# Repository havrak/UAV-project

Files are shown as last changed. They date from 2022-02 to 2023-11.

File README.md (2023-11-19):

# UAV project

This repository contains all resource that comprised my final thesis for my senior year in high school.
Main purpose was to create UAV platform based on Raspberry Pi.

Codebase is this project is rather bad by my current standards and is heavily impacted by the fact it was essentially my first hardware related project.
Not to mention my experience with C++ was rather limited at the time.

Desktop client is written in C++ using Gtk3 and is used to control the drone and display telemetry data.
UI wise it's really bad, and code itself doesn't land much in a way for easy rewrite.

Drone side might fare a bit better, but it's still not great.
Usage of threads is rather questionable and OOP design patterns were a hip new thing for me at the time and not something I was able to use properly.

Thus some parts of codebase are overengineered and some lack any flexibility and don't deserve much other than deletion.

In my 3rd semester of university I've made addition to this project in a shape of proper custom PCB to house drone electronics.

I might rewrite this project in the future, but time is a limited resource and school+work take priority.
Though if rewrite happens, it will be wholly different project.
* camera streaming with gstreamer has never worked as well as I wanted it to
* using Wi-Fi for communication was never ideal (drone was acting as AP)
* codebase and communication protocol needs to be much more open to allow different configurations of hardware
* desktop client needs to be rewritten from scratch and preferably in Qt
* way more robust compilation and deployment process is needed (Kconfig, hierarchical Makefiles, etc.)

# Libraries and toolkits
* [WT901B library](https://github.com/havrak/Raspberry-JY901-Serial-I2C)
* [INA226 library](https://github.com/havrak/raspberry-pi-ina226)
* [PCA9685 library](https://github.com/havrak/PCA9685-rpi)
* [inih (INI Not Invented Here)](https://github.com/benhoyt/inih)
* Gtk3
* crp, fmt
* WiringPi

# Photos

### UAV Photos

whole plane

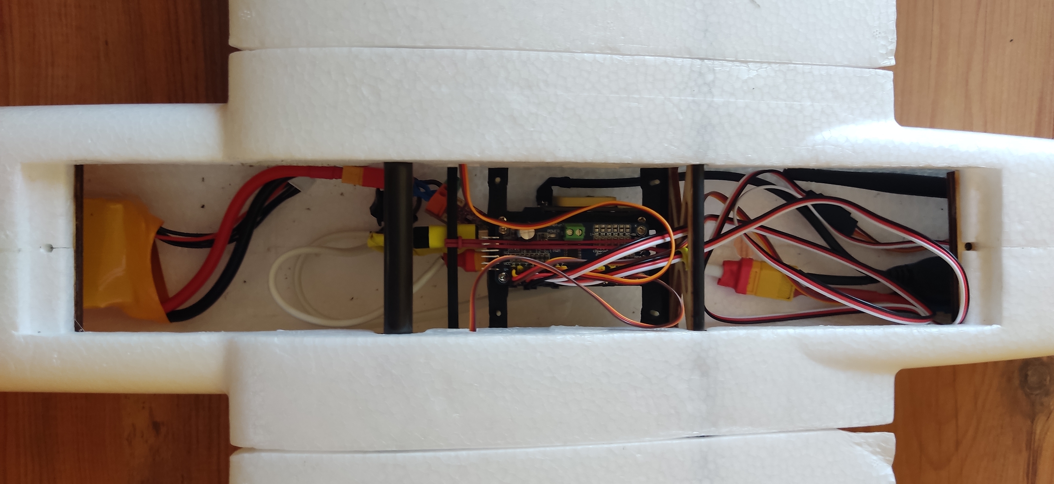
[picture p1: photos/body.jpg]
body detail


### Board

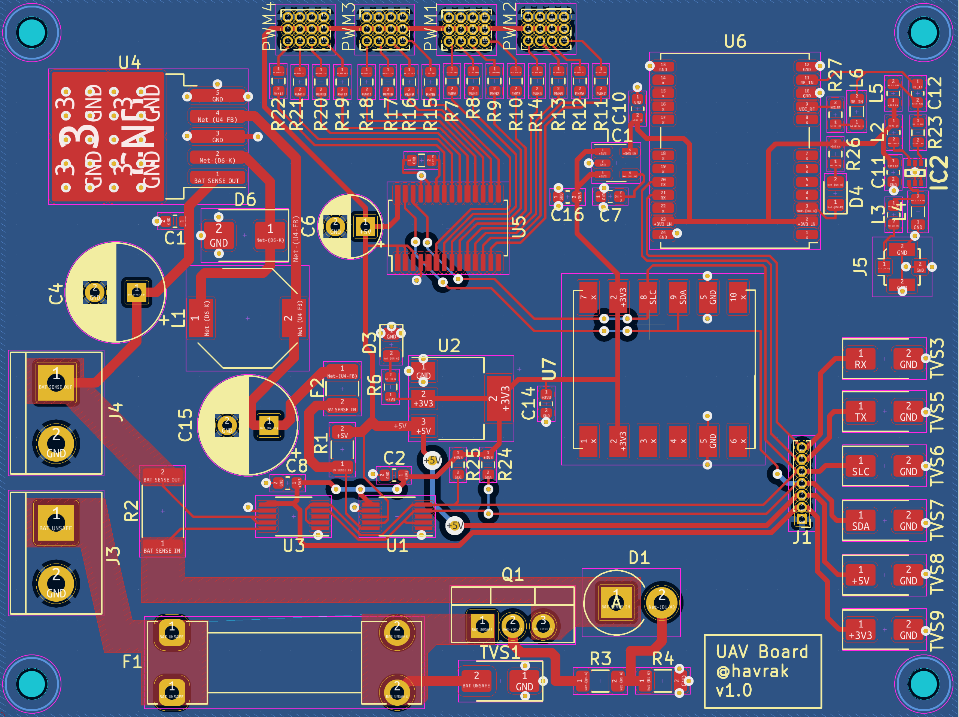
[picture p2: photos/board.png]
board


# Credits
* textures for desktop client originate from [marek-cel/QFlightinstruments](https://github.com/marek-cel/QFlightinstruments)

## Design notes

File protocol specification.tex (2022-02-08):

\documentclass[a4paper,12pt]{report}

\addtolength{\topmargin}{-1.1in}
\setlength\textheight{265mm}
\setlength\textwidth{165mm}
\setlength\oddsidemargin{-2mm}
\setlength\evensidemargin{-2mm}
\usepackage[english]{babel}
\usepackage{tabularx}
\usepackage{longtable}
\usepackage[a-2u]{pdfx}
\usepackage{graphicx}
\usepackage{caption}
\usepackage{lmodern,textcomp}
\usepackage[T1]{fontenc}
\usepackage{fancyhdr}

\def\author{Havránek Kryštof <krystof@havrak.xyz>}

\def\name{UAV Project }

\makeatletter
\def\@makechapterhead#1{
  {\parindent \z@ \raggedright \normalfont
      \huge\bfseries  #1
      \par\nobreak
      \vskip 20\p@
    }}
\def\@makeschapterhead#1{
  {\parindent \z@ \raggedright \normalfont
      \huge\bfseries #1
      \par\nobreak
      \vskip 20\p@
    }}
\makeatother

\renewcommand{\chaptermark}[1]{%
  \markboth{#1}{}}

\fancypagestyle{plain}{
  \fancyhf{}
  \renewcommand{\headrulewidth}{0.4pt}
  \renewcommand{\footrulewidth}{0.4pt}
  \fancyhead[L]{\textbf{\name -- \leftmark}}

  \fancyfoot[L]{\author}
  \fancyfoot[C]{}
  \fancyfoot[R]{\thepage}
}

\begin{document}
\pagestyle{plain}

\chapter{Protocol specification}

\begin{itemize}
  \item protocol desing
    \begin{itemize}
      \item 1st byte -- type of message
      \item 2nd byte -- priority of message (for now for messages with higher priority than 0 new thread will be created)
      \item 3rd and 4th byte -- gives information about size of message -- 3rd is 8 higher bytes, 4th is lower 8 bytes
      \item 5 -- value to be added to check sum -- first 5 bytes need to be divisible by 7
      \item ... -- message
      \item each message is terminated with following sequence -- 0x00, 0x00, 0xFF, 0xFF, 0xFF
    \end{itemize}
  \item ranges
    \begin{itemize}
      \item 0x00 -- 0x20 -- settings management
      \item 0x21 -- 0x40 -- control
      \item 0x41 -- 0xFF -- telemetry
    \end{itemize}
	\item * symbol means code is only used as get request/confirmation
	\item structures used are specified in \verb|<protocol_spec.h>|
\end{itemize}

\subsubsection{Settings}

\begin{center}
  \begin{longtable}{| m{1cm} | m{1.5cm} | m{13cm} | }
    \hline
    0x01 & PI+CL & ping -- empty message send by both sides \\
    0x02 & CL    & restart of system                        \\
    0x03 & CL    & shutdown                                 \\
    0x04 & CL    & disconnect client                        \\
    0x08 & CL    & camera settings                          \\

    \hline
  \end{longtable}
\end{center}

\subsubsection{Control}

\begin{itemize}
  \item these messages are only send by the client to raspberry pi
  \item standart control message will be send continuously -- every few milliseconds (client will have counter to prevent overloading of the server)
  \item we are fine with few of these messages getting lost, as even minor movements will probably result in new message getting send
  \item special message will send confirmation to the client
    \begin{itemize}
      \item client will add these messages to queue, which will be scanned from time to time
      \item if response from server wasn't received in some time client will resend the message
    \end{itemize}

\end{itemize}

\begin{center}
  \begin{longtable}{| m{1cm} | m{1.5cm} | m{13cm} | }
    \hline
    0x21 & CL+PI* & standart control message -- status of analog joystick and shoulder buttons                                                              \\
    0x22 & CL+PI* & special control event -- generated by pressing buttons that don't directly control control surfaces, but are free for further additions \\
    \hline
  \end{longtable}
\end{center}

\subsubsection{Telemetry}

\begin{itemize}
  \item all telemetry, except pwm settings,  is send in intervals
  \item if client want new data immediately it can send message with same header
  \item in such case using priority option is advisable
  \item range above 0x80 is used for errors
\end{itemize}

\begin{center}
  \begin{longtable}{| m{1cm} | m{1.5cm} | m{13cm} | }
    \hline
    0x41 & PI*+CL & status of all i/o                        \\
    0x42 & PI*+CL & general packet including all information \\
    0x43 & PI*+CL & attitude sensor and GPS                  \\
    0x44 & PI*+CL & battery status (reading from ina226)     \\
    0x45 & PI*+CL & pwm setting on servo driver              \\
    0x81 & PI     & general error message                    \\
    \hline
  \end{longtable}
\end{center}

\end{document}

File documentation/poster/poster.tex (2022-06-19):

\documentclass[final]{beamer}

\usepackage[T1]{fontenc}
\usepackage[czech]{babel}
\usepackage{lmodern}
\usepackage[size=a3paper,scale=1.2]{beamerposter}
\usetheme{gemini}
\usecolortheme{mit}
\usepackage{graphicx}
\usepackage{booktabs}
\usepackage{tikz}
\usepackage{pgfplots}
\usepackage{subfigure}
\pgfplotsset{compat=1.14}

% ====================
% Lengths
% ====================

% If you have N columns, choose \sepwidth and \colwidth such that
% (N+1)*\sepwidth + N*\colwidth = \paperwidth
\newlength{\sepwidth}
\newlength{\colwidth}
\setlength{\sepwidth}{0.025\paperwidth}
\setlength{\colwidth}{0.3\paperwidth}

\newcommand{\separatorcolumn}{\begin{column}{\sepwidth}\end{column}}

% ====================
% Title
% ====================

\title{Maturitní práce -- Bezpilotní letadlo}

\author{Havránek Kryštof (Programování, 4.E)}

\institute[shortinst]{Gymnázium, Praha 6, Arabská 14}

% ====================
% Footer (optional)
% ====================

\footercontent{
  \href{https://github.com/havrak/UAV-project}{https://github.com/havrak/UAV-project} \hfill
  Březen 2022 \hfill
  \href{mailto:krystof@havrak.xyz}{krystof@havrak.xyz}}
% (can be left out to remove footer)

% ====================
% Logo (optional)
% ====================

% use this to include logos on the left and/or right side of the header:
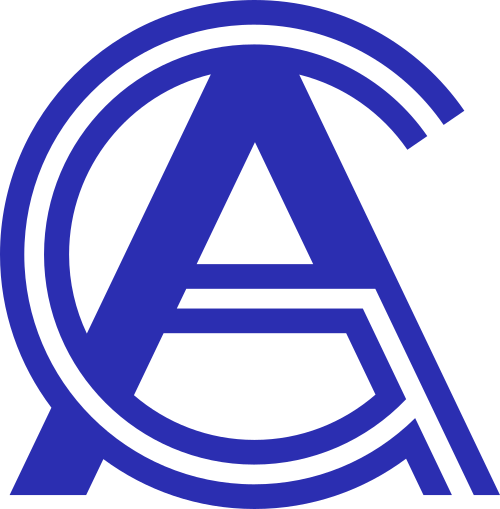
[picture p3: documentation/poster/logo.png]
\logoleft{}
% \logoleft{\includegraphics[height=7cm]{logo2.pdf}}

% ====================
% Body
% ====================

\begin{document}

\begin{frame}[t]
  \begin{columns}[t]
    \separatorcolumn

    \begin{column}{\colwidth}

      \begin{block}{Abstrakt}

        Cílem práce je vytvoření bezpilotního letadla a doprovodného systému umožnující pilotovi letadlo dálkově ovládat.
        Pilot by měl mít možnost sledovat živý přenos z kamery a získávat doprovodnou telemetrii.
        Celý program by měl být rychlý, aby ovládání bylo s co nejmenší odezvou, a napsaný stylem umožnující další vývoj.

      \end{block}

      \begin{block}{Použité technologie}

        \begin{figure}
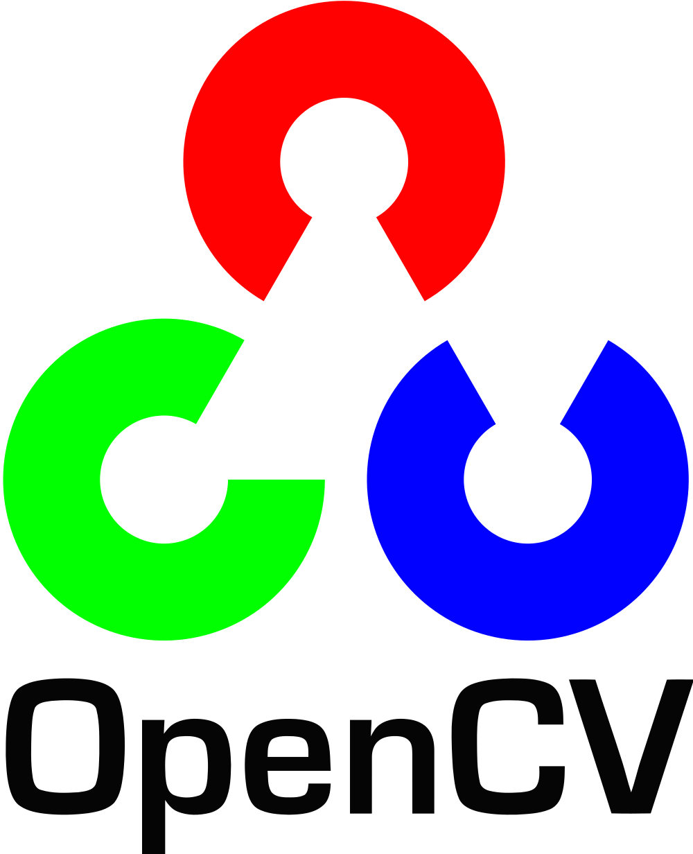
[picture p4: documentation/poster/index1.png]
          \subfigure{}
          \hfill
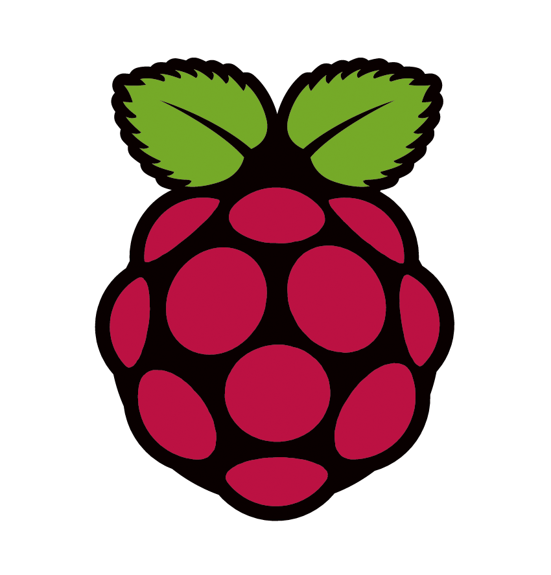
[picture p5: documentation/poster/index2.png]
          \subfigure{}
          \hfill
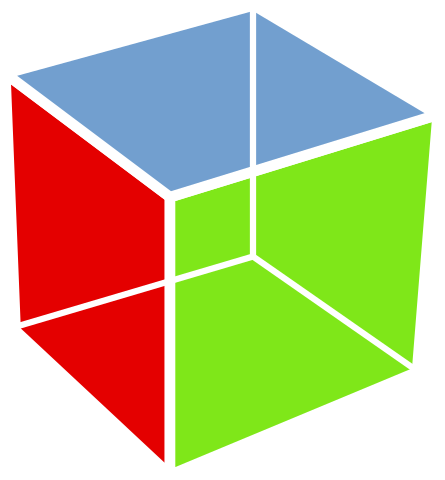
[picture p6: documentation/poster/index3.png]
          \subfigure{}
          \hfill
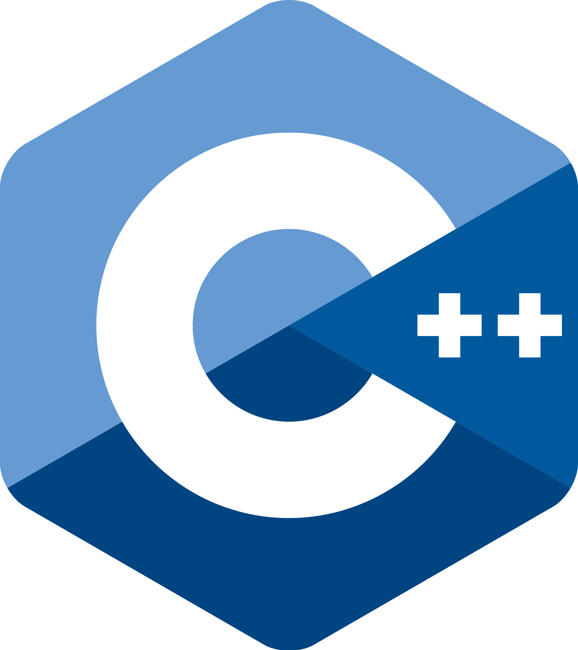
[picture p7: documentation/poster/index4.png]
          \subfigure{}
          \hfill
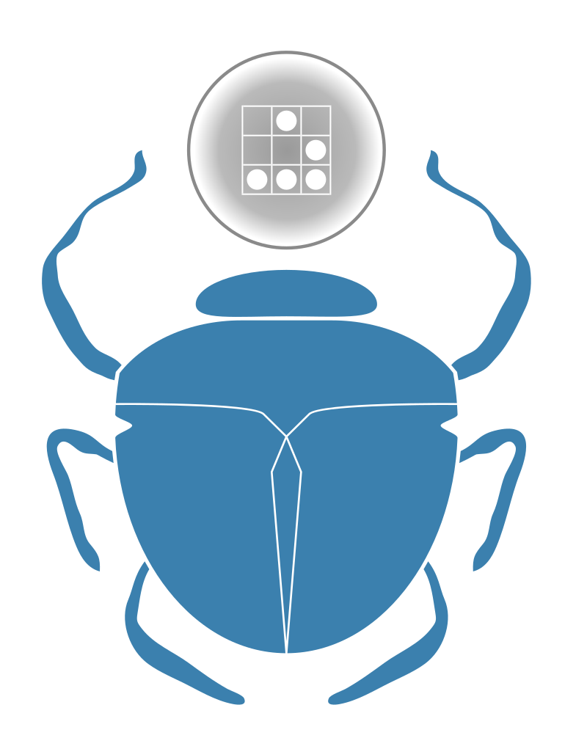
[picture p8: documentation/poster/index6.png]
          \subfigure{}
          \hfill
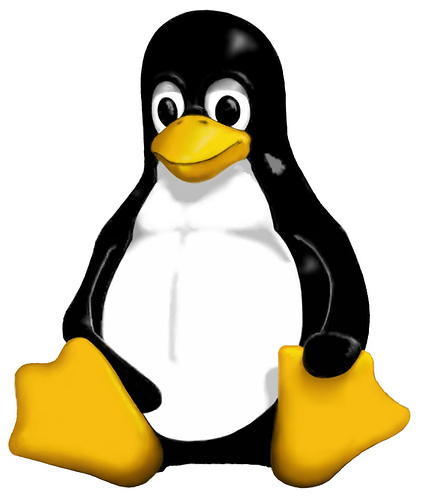
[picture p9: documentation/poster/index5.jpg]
          \subfigure{}
          \hfill

        \end{figure}

			Celý projekt je psán v jazyce C++ a vyvíjen primárně pro zařízení s operačním systémem Linux.
			V případě ovládací softwaru je port na další OS možný, jelikož používaný grafický toolikt je multiplatformní.

      \end{block}

      \begin{block}{Komunikační protokol}

				Obě části projektu mezi sebou komunikují prostřednictvím protokolu postaveném na rodině TCP.
				Letadlo na sebe přejímá roli serveru, umožňuje tak několik clientů -- telemetrii z dronu lze tak monitorovat z několika počítačů.
				Případně si lze \uv{předávat} kontrolu nad dronem mezi počítači.

				Protokol se stará o tři důležité části řízení letadla.
				Je schopen na dálku drona konfigurovat -- například spustit kameru.
				Dále předává informace letadlu z herního, kterým se letadlo ovládá.
				V neposlední řadě umožňuje letadlu posílat zpět telemetrii, případě chybové hlášky.
				Telemetrie se pak zobrazuje pilotu v ovládacím softwaru, chybové hlášky se manifestují prostřednictvím dialogových oken.
      \end{block}

      \begin{block}{Fotografie letadla}

				\begin{figure}[h]
					\centering
					
				\end{figure}

      \end{block}

    \end{column}

    \separatorcolumn

    \begin{column}{\colwidth}

      \begin{block}{Hardware a software letadla}

				Dron je postaven na jednodeskovém počítači Raspberry Pi.
				Systém je primárně určen pro moduly ze série Raspberry Pi Zero.
				Primárně se však tak je činěno z důvodu prostorových omezení řad koster letadel.
				Teoreticky může projekt fungovat na libovolném počítači Raspberry Pi.

				Jelikož používá specifické funkce pro interakci s hardwarem není možné projekt rozeběhnout na dalších malých počítačích.
				Stejně tak je projekt závislý na knihovnách a driverech, které jsou standardní součástí operačního systému raspbian.

				Projekt využívá hned několik periférií, těma jsou:

        \begin{enumerate}
          \item WT901B -- devíti-osý polohový senzor -- počítá yaw, roll a pitch
          \item PCA9865 -- modul pro ovládání servo motorů
          \item INA226 -- voltmetr/ampérmetr pro získání dat z baterie
					\item ublox NEO 7M GPS -- GPS modul
					\item Beatles 40A ESC -- Electronic Speed Control -- umožňuje ovládat hlavní motor
        \end{enumerate}

      \end{block}

      \begin{block}{Schéma zapojení}

				Schéma zapojení je relativně přímočaré.
				Většina komponent s Raspberry PI komunikuje prostřednictvím I2C spojený a je napojena na piny 3 a 5.
				Vzhledem k počtu komponent jsou napojené na 3.3V drain přes 4.7 $\Omega$ rezistory.
				Výjimku představuje GPS, která využívá sériovou linku.

				Raspberry Pi a další sensory nejsou napájené prostřednictvím ESC, ale z přímo baterie prostřednictvím DC/DC step down covertru.

				\begin{figure}[h]
					\centering
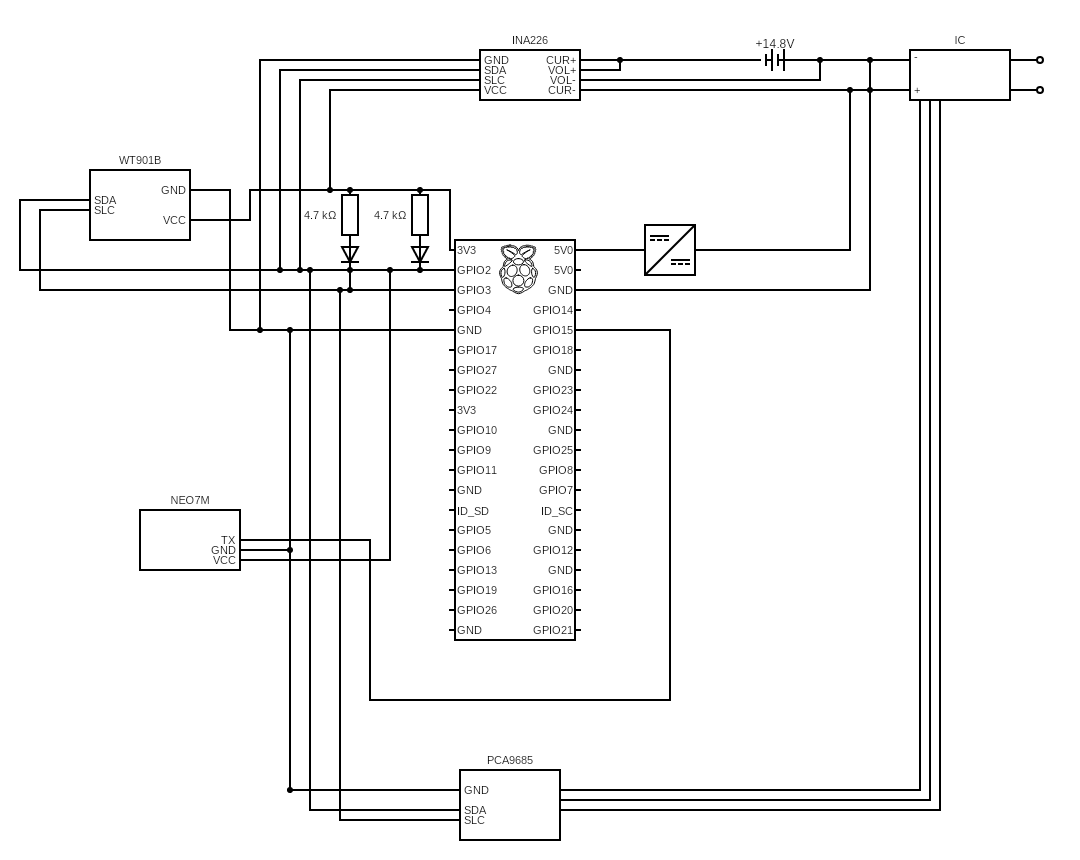
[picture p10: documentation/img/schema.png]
					
				\end{figure}

      \end{block}

    \end{column}

    \separatorcolumn

    \begin{column}{\colwidth}

			\begin{block}{Zapojení}

				Většina komponent je umístěna na pájivém poli, které se přímo nasazuje na samotné Raspberry Pi.
				Voltmetr se nachází v ocasní části letadla, je tak separátně od většiny komponent a připojuje se k nim prostřednictvím USB konektoru.

				K Raspberry Pi je také připojen Wi-Fi Adaptér, který poskytuje silnější signál než integrovaný Wi-Fi čip.
				To jest potřeba, jelikož dron funguje jako router.

				\begin{figure}[h]
					\centering
					
				\end{figure}

			\end{block}

			\begin{block}{Ovládání}

				Letadlo se ovládá pomocí ovladače od herní konzole Xbox One.
				Poloha prvků ovladače je posílána přímo na letadlo, kde se teprve interpretuje.
				Nejprve se přepočítají polohy joysticků na čtverec a pak se vyvodí polohy 4 ovládacích ploch (2 $\times$ aileron, 2 $\times$ ruddervator)

				\underline{Autopilot:}

				Letadlo je schopno držet svojí letovou hladinu bez zásahu pilota.
				K tomu slouží jednoduchý autopilot postavený na dvou PID (proporčně-integračně-derivačních) kontrolérech.
				Jeden se snaží minimalizovat yaw letadla, druhý pak jeho pitch.

			\end{block}

      \begin{block}{Software pro řízení letadla}

			\begin{columns}[T]
				\begin{column}{.4\textwidth}
					Dron se řídí prostřednictvím jednoduché aplikace pro počítač.
					Grafické prostředí je psáno s pomocí knihovny Gtk3, dobře tak ladí s většinou dalších oken na Linuxu.
					Aplikace aktuálně pouze zobrazuje telemetrii z dronu a záznam z jeho kamery.
					Další funkce nebyly zatím implementovány.

				\end{column}
				\begin{column}{.6\textwidth}
			\begin{figure}[h]
				\centering
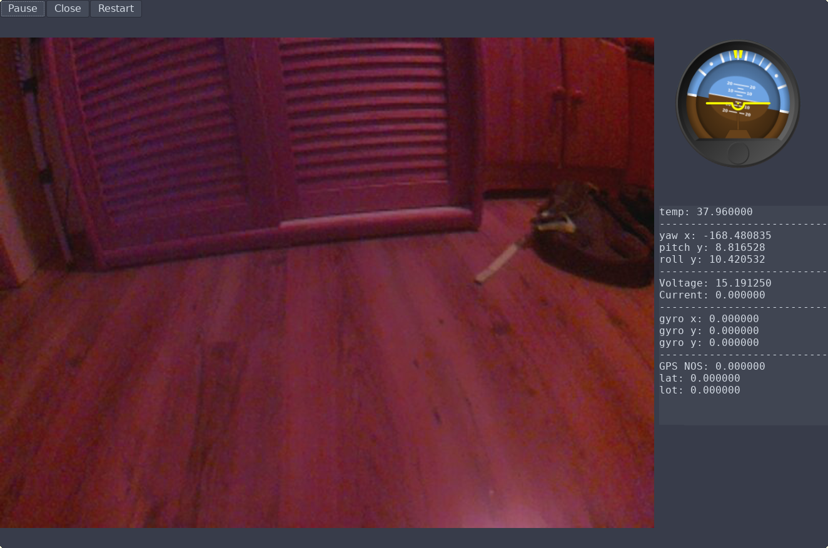
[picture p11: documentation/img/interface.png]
				
			\end{figure}

				\end{column}
			\end{columns}

      \end{block}

    \end{column}

    \separatorcolumn
  \end{columns}
\end{frame}

\end{document}

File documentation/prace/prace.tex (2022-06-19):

\documentclass[a4paper,oneside,12pt]{report}
\setlength\textwidth{155mm}
\setlength\textheight{247mm}
\setlength\topmargin{-10mm}
\setlength\headheight{0mm}
\setlength\oddsidemargin{05mm}
\setlength\evensidemargin{05mm}
\let\openright=\clearpage

%% Vytváříme PDF/A-2u
\usepackage[a-2u]{pdfx}

%% Přepneme na českou sazbu a fonty Latin Modern
\usepackage[czech]{babel}
\usepackage[utf8]{inputenc}
\usepackage{lmodern}
\usepackage[T1]{fontenc}
\usepackage{textcomp}

\usepackage{amsmath}						% rozšíření pro sazbu matematiky
\usepackage{amsfonts}						% matematické fonty
\usepackage{amsthm}							% sazba vět, definic apod.
\usepackage{bbding}							% balíček s nejrůznějšími symboly (čtverečky, hvězdičky, tužtičky, nůžtičky, ...)
\usepackage{bm}									% tučné symboly (příkaz \bm)
\usepackage{graphicx}						% vkládání obrázků
\usepackage{fancyhdr}						% možnost stylizovat záhlaví
\usepackage{fancyvrb}						% vylepšené prostředí pro strojové písmo
\usepackage{indentfirst}				% zavede odsazení 1. odstavce kapitoly
\usepackage[nottoc]{tocbibind} 	% zajistí přidání seznamu literatury,
\usepackage{icomma}         		% inteligentní čárka v matematickém módu
\usepackage{dcolumn}        		% lepší zarovnání sloupců v tabulkách
\usepackage{booktabs}       		% lepší vodorovné linky v tabulkách
\usepackage{paralist}       		% lepší enumerate a itemize
\usepackage{caption}						%	popisky
\usepackage{dirtree}						% strom souborů
\usepackage{minted} 						% vkládání kódu
\usepackage[bottom]{footmisc}  	% poznámky pod čarou vespod
\usepackage{bibentry} 					% citace přes celé heslo, používáno u první citace z jednoho zdroje
\usepackage{xurl}								% umožní url zalomit všude
\usepackage{hyperref} 					% odstranění červených okrajů v obsahu
\nobibliography*

\usepackage{color}
\usepackage{natbib}

\definecolor{pblue}{rgb}{0.13,0.13,1}
\definecolor{pgreen}{rgb}{0,0.5,0}
\definecolor{pred}{rgb}{0.9,0,0}
\definecolor{pgrey}{rgb}{0.46,0.45,0.48}
\renewcommand{\baselinestretch}{1.5}
%%% Údaje o práci

\def\NazevSkoly{Gymnázium, Praha 6, Arabská 14}
% Název oboru včetně počátečního 'Obor'.
\def\NazevOboru{Programování}

% Název práce v jazyce práce (přesně podle zadání)
\def\NazevPrace{Bezpilotní letadlo}

\def\NazevPraceShort{Bezpilotní letadlo}
% Název práce v angličtině
\def\NazevPraceEN{Drone}

% Název práce v němčině
\def\NazevPraceDE{Drohne}

% Jméno autora
\def\AutorPrace{Havránek Kryštof 4E}

% Rok odevzdání
\def\RokOdevzdani{2022}
% Měsíc odevzdání
\def\MesicOdevzdani{Březen}

% Vedoucí práce: Jméno a příjmení s~tituly
\def\Vedouci{ing. Daniel Kahoun}

% Nepovinné poděkování (vedoucímu práce, konzultantovi, tomu, kdo
% zapůjčil software, literaturu apod.)
\def\Podekovani{%
  \textbf{Poděkování}
}

% Abstrakt (doporučený rozsah cca 80-200 slov; nejedná se o zadání práce)
\def\Abstrakt{%
Cílem práce je vytvořit autonomní letadlo, které bude pilot dálkově ovládat prostřednictvím softwaru na počítači.
Z letadla bude během provozu dostávat potřebnou telemetrii a přesnos videa.
Software by měl být napsán stylem, který umožňuje budoucí vývoj.
}

\def\AbstraktEN{%
The aim of the work is to create an unmanned aerial vehicle system which will be controled remotely by the pilot from software on a computer.
Pilot should recive all the necessary telemetry in addition to video stream from the aircraft.
Software should be written in a style that allows for future development.
}
\def\AbstraktDE{%
Ziel der Arbeit ist es, ein unbemanntes Luftfahrzeugsystem zu schaffen, das vom Piloten aus der Ferne von einer Software auf einem Computer gesteuert wird.
Der Pilot sollte alle erforderlichen Telemetrie und Videostreams vom Flugzeug erhalten.
Software sollte in einem Stil geschrieben werden, der eine zukünftige Entwicklung ermöglicht.
}
% 3 až 5 klíčových slov (doporučeno), každé uzavřeno ve složených závorkách
\def\KlicovaSlova{%
  (UAV), (Gtk), (C++), (Raspberry Pi zero 2)
}
\def\KlicovaSlovaEN{%
  (UAV), (Gtk), (C++), (Raspberry Pi zero 2)
}
\def\KlicovaSlovaDE{%
  (UAV), (Gtk), (C++), (Raspberry Pi zero 2)
}

%% Balíček hyperref, kterým jdou vyrábět klikací odkazy v PDF,
%% ale hlavně ho používáme k uložení metadat do PDF (včetně obsahu).
\hypersetup{unicode}
\hypersetup{breaklinks=true}
\hypersetup{pdfborder=0 0 0}

%% Definice různých užitečných maker (viz popis uvnitř souboru)
\include{makra}

%% Titulní strana a různé povinné informační strany
\fancypagestyle{plain}{
  \fancyhf{}
  \renewcommand{\headrulewidth}{0.4pt}
  \renewcommand{\footrulewidth}{0.4pt}
  \fancyhead[C]{}
  \fancyhead[L]{Maturitní práce -- \NazevSkoly}
  \fancyhead[R]{\NazevPraceShort}
  \fancyfoot[L]{Vypracoval: \AutorPrace$\,\,$(\NazevOboru)}
  \fancyfoot[C]{}
  \fancyfoot[R]{\thepage}
}

\begin{document}

\include{titulka}

\tableofcontents

\newpage

\include{uvod}
\pagenumbering{arabic}
\setcounter{page}{1}

\chapter{Rozložení práce}

Práci lze rozdělit na dvě základní komponenty.
První část software běží na počítači přes který se bezpilotní letadlo ovládá, druhá na samotném dronu.
Obě části jsou psané v jazyce C++.

Software pro počítač používá grafickou knihovnu Gtk3 a byl vyvíjen primárně na operačním systém Linux.
Gtk3 je multiplatformní toolkit, port na další operační systémy je tak možný a kód je psán stylem, aby toto umožnil.

Jádro samotného dronu představuje malý počítač Raspberry Pi Zero 2.
Vyšší výkon verze Zero 2 není nutný pro fungování, práce může fungovat na libovolném Raspberry Pi.
Program využívá jen zlomek zdrojů  a to jak po stránce paměti, tak výpočetního výkonu.

Obě části mezi sebou komunikují prostřednictvím protokolu založeném na rodině TCP.
Přenos videa je zprostředkovávám pomocí UDP.
Samotné video je kódováno do jpg, v porovnání s dalšími styly přenosu byla u jpg menší latence.

Rychlost latence byla testována pomocí jednoduché aparatury, kde malý kód četl obrazovku, kde byl zobrazen záznam z kamery, a ovládal LED na ESP32.
Systém jednoduše měřil za jak dlouho se na obrazovce objevila rozsvícená dioda (Předem vybraný pixel změnil barvu) poté co skript poslal příkaz k rozsvícení

\section{Komunikační protokol}

Pilotův počítač a Raspberry mezi sebou komunikují prostřednictvím jednoduchého protokolu postaveném na rodině TCP.
Raspberry Pi přebírá roli serveru, to mimo jiné umožňuje, aby bylo letadlo ovládáno z více stanic.

Protokol prozatím není zašifrovaný a nepočítá také s nevalidními daty.
Šifrování však není příliš nutné -- dron a počítač operují na vlastní síti, kde Raspberry Pi funguje jako Wi-Fi Access--Point.
Struktura protokolu ovšem nabízí možnost jednoduše implementovat symetrickou kryptografii.
Ta by byla zcela postačující, její klíče by byly uloženy v konfiguračních souborech programu.

\subsection{Struktura protokolu}

Každý packet začíná hlavičkou o velikosti 5 bytů.

\begin{enumerate}
  \item typ zprávy
  \item priorita -- Program prozatím prioritu nebere v potaz.
  \item 8 horních bitů velikosti zprávy
  \item 8 dolních bitů velikosti zprávy
  \item dopočet do kontrolního součtu -- součet čísel v hlavničce musí být dělitelný sedmi.
\end{enumerate}

Po hlavičce následuje samotná zpráva zakončená posloupností pěti bytů -- 0x00, 0x00, 0xFF, 0xFF, 0xFF.
Zakončovací řetězec slouží pro případ, kdy nějaký packet nedorazí, či příchozí zpráva byla nějak poškozena.
Nastane li tato situace, program postupně čte byty ze socketu a hledá tuto sekvenci.
Maximální délka zprávy je půl kilobytu, samotná data jsou posílána v balíčcích o maximální velikosti 250 bytů.
Omezení velikosti zprávy je zavedeno hlavně kvůli šetření paměti -- program má pro každého klienta vytvořené jedno pole, do kterého se musí vejít celá zpráva.

Protokol funguje na základě posílání struktur, definovaných v \verb|protocol_spec.h|.
Pro odeslání dat je nejprve nutné nahrát data do struktury.
Dále se z těchto dat vytvoří tzv. SendingStructure, které se odešle do thread poolu, ten zprávu eventuálně odešle.
Při přijímání se data načítají do bufferu spojeným s klientem, ze kterého se později zkopírují objektu ProcessingStructure.
Příslušná část programu si pak data přes memcpy opět zkopíruje do příslušné struktury.

Pro příjem a zpracování zpráv slouží dva thread pooly -- SendingThreadPool a ProcessingThreadPool.
Jednotlivé části programu tak nemusí čekat, až se uvolní socket, aby se mohla data odeslat, či čekat na jejich zpracování pro přijetí dalších.
Speciální případem je zpracování příkazů, které přímo ovládají pohyb letadla.
Pro ovládaní existuje samostatné vlákno, které příkazy vykonává sekvenčně.
Také je implementován mechanismus, kde příliš staré příkazy se nevykonají.

Program sleduje aktivitu na socket pomocí příkazu select.
Při běžné provozu tak většina vláken komunikace spí a zátěž není příliš velká.

Z hlediska programové stránky jsou veškeré součásti komunikace implementovány jako singletony.
Program je tak řešen, aby umožnil jednoduše odesílat zprávy z různých částí programu.

\subsection{Specifikace protokolu}

Protokol obsluhuje tři základní části provozu dronu -- nastavení, ovládaní a telemetrie.
Pro nastavení je vyhrazen rozsah od 0x00 po 0x20 a zahrnuje věci, jako je odpojení klienta, nastavení kamery, či restart.

Další kategorii představuje ovládaní, pro které je vyhrazen prostor mezi 0x21 až 0x40.
Projekt implementuje dva základní typy -- standardní ovládaní (pohyb joysticku, atd.) a speciální.
Standardní slouží pro prosté manuální ovládání dronu.
Speciální například resetuje polohoměr, či zapíná autopilota.

Poslední kategorií je telemetrie, která má zbytek rozsahu do 0xFF.
Tu ve standardním chování posílá Raspberry každých pár stovek milisekund.
Pokud klient potřebuje aktuálnější data, může si je vyžádat odesláním zprávy o stejném typu, jako jsou požadovaná data.
Speciální případ představují chybové hlášky, které vyžádat pochopitelně nejdou a pilotovi se zobrazují v dialogovém okně.

\section{Konfigurace}

Některé vlastnosti programu, lze specifikovat v konfiguračním souboru.
Ten se nachází ve složce \verb|$HOME/.config/uav_control/config.ini| u počítačů s operačním systémem postaveným na UNIXu.
Soubor se psán stylem INI, který je lehce čitelný a~vhodný na malý rozsah konfigurace.
Pro zpracování je použita knihovna inih\footnote{\bibentry{inih}}.

Konfigurace je nutná jak na straně pilota, tak na straně dronu.
U pilota se nastavuje například typ ovladače, či port, na kterém má být přijímán záznam z kamery.
Konfigurace na straně dronu určuje například, jaká je orientace polohového senzoru, či rozložení křídel.

V aktuální verzí se konfigurační soubor nevygeneruje sám, program však má definované hodnoty, ke kterým se uchýlí v jeho absenci.

\chapter{Hardware a Raspberry Pi}

Jádro samotného letadla tvoří malý počítač Raspberry Pi Zero 2.
Ostatní periférie jsou: polohový senzor WT901B, voltmetr a ampérmetr INA226, ovladač na serva PCA9865, ublox NEO-7M GPS modul a BEATLES 40A ESC (Electronic speed control).
Vše s výjimkou GPS komunikuje s Raspberry Pi prostřednictví I2C protokolu.
GPS modul využívá sériovou linku.

Senzor WT901B sice podporuje přímé napojení GPS senzoru, při pokusu o konfiguraci senzoru však přestala fungovat sériová komunikace obecně.

Systém má dva přívody proudu -- hlavní motor a serva jsou napájeny prostřednictví ESC.
To však nebylo schopné poskytovat dostatečný proud pro Raspberry Pi a senzory na něj napojené.
Z baterie je tak vyvedená linka napojená na step down converter, který 14.8 V sníží na 5V.
Tento výstup je pak připojen k 5V pinu Raspberry Pi.

\begin{figure}[h]
  \centering
  
  \caption[Schéma zapojení obvodu]{Schéma zapojení obvodu}
\end{figure}

\newpage

Většina komponentů je umístěna na pájivé pole, které lze jednoduše nasadit na Raspberry Pi.
Výjimku představuje voltmetr/ampérmetr, který je volně a v letadle se nachází v ocase.
Ke zbytku se připojuje přes koncovku USB, ostatní koncovky (tj. ty pro napájení) jsou XT60.

\begin{figure}[h]
  \centering
  
  \caption[Detail Raspberry Pi]{Řídící jednotka}
\end{figure}

\begin{figure}[h]
  \centering
  
  \caption[Detail těla dronu]{Detail těla dronu}
\end{figure}

\begin{figure}[h]
  \centering
  
  \caption[Celý dron]{Celý dron}
\end{figure}

Kostrou dronu je model Mini Talon od čínské společnosti X-UAV.
Rozpětí křídel je 130cm délka 85cm.
Jedná se o tzv. V-Tail konfiguraci, ocas tedy nemá standardní tři kontrolní plochy, ale pouze dvě.
V aktuální verzi program má naimplementované ovládání pouze pro tuto konfiguraci.

\newpage

\section{Program}

\begin{figure}[h]
  \dirtree{%
    .1 drone\_software.
    .2 libraries.
    .3 Raspberry-JY901-Serial.
    .3 raspberry-pi-ina226.
    .3 rpidmx512-Lib-PCA9685.
    .2 include.
    .3 battery\_interface.h.
    .3 camera\_streamer.h.
    .3 communication\_interface.h.
		.3 config.h.
    .3 generic\_PID.h.
    .3 gps\_interface.h.
    .3 imu\_interface.h.
    .3 protocol\_spec.h.
    .3 servo\_control.h.
    .3 telemetry.h.
    .2 src - implemetation of  header files.
  }
  \caption[Struktura souborů na dronu, vlastní tvorba]{Struktura souborů frontend}
\end{figure}

Program na Raspberry Pi používá tři základní knihovny pro komunikaci s WT901B, INA226 a PCA9685.
Přenos z kamery pak zprostředkovává OpenCV, který jako backend používá gstreamer.
V budoucnu je tak možné přidat analýzu videa přes OpenCV přímo na Raspberry Pi -- například detekce věcí na obrazu.

\section{Interface s Hardwarem}

Jak už bylo řečeno, s hardwarem Raspberry komunikuje prostřednictví I2C spojení a sériové linky.
Pro zpracování dat z INA226 a WT901B byly napsány nové knihovny.
Jelikož knihovny pro Raspberry Pi totiž buďto neexistovaly, nebo nebyly zdaleka kompletní.

Knihovna pro WT901B vznikla forkem knihovny pro Arduino\footnote{\bibentry{WT901BL}} a byla předělána v~souladu s dokumentací protokolu\footnote{\bibentry{WT901B}}.
Kvůli problémům se senzorem byla i dopsána I2C komunikace, kterou původní knihovna neimplementovala.

V případě senzoru INA226 bylo forknuto demo\footnote{\bibentry{INA226L}} z GitHubu a dopsáno v plnohodnotnou knihovnu.

Obě knihovny využívají knihovnu wiringPi.
Ta byla koncem roku 2021 spolu s~vydáním raspbian bullseye označena ze deprecated.
Existuje, ale fork, kde se na vývoji dále pokračuje.
Samotné wiringPi je navíc defacto pouze wrapper pro přímý přístup k~smbus.

Vzhledem k přímočarosti výstupu z GPS modulu je celá implementace přímo součástí hlavního kódu.
Program zpracovává GPGGA packet, který obsahuje veškerá důležitá data.
Zpracování dalších packetů nebylo pro práci podstatné.

Knihovna pro ovládaní server byla lehce přepsána pro potřeby tohoto projektu.
Původní verze knihovny\footnote{\bibentry{PCA9865}} využívala driver bcm2835 ke komunikaci s I2C linkou.
Docházelo tak ke kolizím s časováním, které vedly k narušení integrity dat ze senzorů.
Byla tak přepsána za účelem, aby také používala wiringPi.

\section{Organizace v kódu}

Z programu se k perifériím přistupuje přes několik singletonů -- ImuInterface pro WT901B, BatterInterface pro INA226, GPSInterface pro ublox NEO 7M a ServoControl pro PCA9865.
Důvod řešení přes singletony je opět stejný jako u komunikace.
Data ze senzorů jsou potřeba v různých částech programu a reálně reprezentují pouze jeden senzor.

Díky tomu program nepotřebuje jednu centrální třídu, která by vše organizovala.
Mizí tak problémy s řadou lokálních proměnných a nutností je udržovat aktuální.
Jelikož celý program je vícevláknový, implementují tak singletony ochranu před kolizí několika vláken a vzniku nevalidních dat.

Data ze senzorů, jsou agregována v třídě telemetry.
Ta se stará o nastavení všech senzorů a zároveň zajišťuje vytvoření packetů pro odeslání klientovi.
Ze stejných důvodů jako další třídy, i telemetry je implementována jakožto singleton.

O přístup ke kameře se stará třída CameraStreamer.
Ta se vytváří dynamicky na základě požadavku od klienta.
Jelikož aktuálně není implementována žádná analýza obrazu z kamery přímo na Raspberry Pi, proces stremu vznikne jako fork procesu, ve kterém je spuštěn stream.

\section{Ovládání letadla}

O ovládání kontrolních ploch a motoru se stará třída ServoControl.
V aktuální podobě přímo zpracovává data z ovladače, která posílá server.
Není tak možné jednoduše změnit jaké ovládací prvky ovladače, budou letadlo ovládat.

Na počátku zpracování nových příkazů jsou hodnoty analogové páčky přepočítány do čtvercové plochy.
Standardně se totiž mapují ovladače na kruh -- páčka čistě nahoru tak má výrazně vyšší hodnotu osy Y, než páčka pod úhlem 45 stupňů, to i přesto, že urazily stejnou vzdálenost.
Bez této korekce ovládání působilo velmi neresponzivně, kdy praktické byly pouze polohy jih, sever, západ, východ.

V případě konfigurace ocasu do tvaru písmena V je interpretace ovládání relativně jednoduchá.
Ocasní plochy (Ruddervator) ovládají pitch (klopění) a yaw (bočení).
Plochy na křídlech nastavují roll (klonění) letadla, teoreticky mohou ovládat i yaw, v tomto případě to však nebylo třeba.

\subsection{Autopilot}

Projekt implementuje i jednoduchého autopilota, který je schopen držet letovou hladinu.
Vyrovnávání řeší dva proporčně-integračně-derivační ovladače, které se snaží minimalizovat chybu.
Jeden minimalizuje odchylku v klopení, druhý pak odchylku v~klonění.
Roll minimalizovat není třeba -- pro roll musí být letadlo nakloněno.

Teoreticky by mohlo jít tento sytém rozšířit aby se snažil minimalizovat odchylku nikoliv od původního směru, ale od pomyslného bodu určeného souřadnicemi GPS.
Letadlo by tak nejenže letělo více rovně (aktuálně je autopilot náchylný na změnu posunutí v příčné ose), ale mohlo byu samo doletět na specifikovaný bod.

\chapter{Client na ovládání}

Ovládací klient pro počítač je stejně jako software pro Raspberry Pi psán v jazyce C++.
K vykreslení uživatelského prostředí je použita grafická knihovna Gtk3.
Konkrétně pak wrapper gtkmm, který zprostředkovává funkce Gtk z jazyka C++.
Ačkoliv byl celý systém vyvíjen pro Linux je možný port na další operační systémy, jelikož Gtk je multiplatformní toolkit.

\begin{figure}[h]
  \centering
  
  \caption[Grafické prostředí aplikace]{Grafické prostředí aplikace}
\end{figure}

V aktuální verzi je grafická stránka aplikace relativně strohá.
Většinu obrazovky zabírá výstup z kamery a polevé straně se nachází informace z telemetrie.
Ty jsou prozatím zprostředkovány promocí umělého horizontu a textového výpisu.

Kvůli absenci předešlých zkušeností s Gtk toolkitem a nástrojem glade na vytváření uživatelského prostředí byla použita boilerplate aplikace\footnote{\bibentry{BoilerplateGUI}}.
Boilerplate mimo jiné u ukazoval propojení s webkamerou, část logiky okolo zobrazení obrazu tak byla využita pro stream z Raspberry Pi.
Systém byl však udělán více robustní a byla přidána například podpora zvětšení velikosti obrazu v závislosti na velikosti okna.

Grafika umělého horizontu je generována prostřednictví knihovny Cairo.
Ta je na manipulaci s obrázky je mnohem efektivnější, než nástroje standardně nabízené v Gtk.
Samotné textury pro umělý horizont byly převzaty z jiného projektu\footnote{\bibentry{Texture}}.
Jejich použití je v souladu s MIT licencí, pod kterou jsou distribuovány.

\section{Organizace kódu}

\begin{figure}[h]
  \dirtree{%
    .1 desktop\_client.
    .2 img.
    .2 include.
		.3 camera.h.
    .3 communication\_interface.h.
		.3 config.h.
    .3 control\_interpreter.h.
    .3 controller\_interface.h.
    .3 drone\_telemetry.h.
    .3 linux\_controller\_implementation.h.
    .3 main\_window.h.
    .3 protocol\_spec.h.
    .2 src - implementation of header files.
  }
  \caption[Struktura souborů klienta]{Struktura souborů klienta}
\end{figure}

Veškerá logika grafického prostředí je koncentrována v souboru \verb|main_window.h|.
Knihovna Gtk není příliš vstřícná objektově orientovanému programování a efektivní granularizace kódu se dosahuje těžce.
Jelikož aktuální velikost kódu není příliš velká, nepředstavuje tato limitace větší problém.
Přesto je aktuální organizace dočasným řešením, zvláště pak v případě logiky týkající zpracování kamery.

Podobně jako na Raspberry Pi i počítačový klient má soubor, ve kterém je agregována veškerá telemetrie.
Při získání nové telemetrie třída také požádá Gtk o zavolání metody, která přepíše data na obrazovce.

Soubory \verb|protocol_spec.h| a \verb|communication_interface.h| se starají o implementaci komunikačního protokolu.
Ze stránky kódu jsou velmi podobné implementaci, která je na Raspberry Pi.
Součástí kódu s komunikací je i třída ControllerDroneBridge, ta zprostředkovává interpretaci událostí z ovladače a posílá jeho aktuální rozložení Raspberry Pi.

\section{Zpracování data z ovladače}

Zpracování dat z ovladače je koncipované okolo faktu, že systém nemá standardně callbacky na události vyvolané ovladačem.
Přístup přes callbacky je však relativně přívětivý, a tak je tato funkcionalita implementována v programu.
V souboru \verb|linux_contr|
\verb|oller_implementation| je proto definovaný cyklus, který běží v sólo vlákně.
Ten čte z~file descriptoru a v případě větší změny na ovladači si data zapíše do vlastní struktury.
Data ve struktuře přímo neodpovídají vstupu z ovladače -- v případě os jsou posunuté o maximální hodnotu (32767).
Díky tomu je zabráněno záporným hodnotám, které by mohly dělat problémy v matematice aplikované na datech

Při zapsání nového stavu ovladače se zároveň vygeneruje událost, která se pošle všem observerům.
Logika pro návrhový vzor observer je deklarovaná v třídě \verb|Controlle|
\verb|rInterface|.
Toto rozdělení konkrétní implementace ovladače od základní deklarace prostředí pro přístup k ovladači umožňuje lehce implementovat komunikaci s ovladačem pro další operační systémy.

Veškeré observery musí implementovat abstraktní třídu \verb|ControlInterpreter|.
Aktuálně se může tento systém jevit jako zbytečně složitý.
Byl však vytvořen s ohledem k budoucí funkcionalitě projektu.
Ovladačem by totiž mělo být možné ovládat celé uživatelské prostředí -- pohyb na D-Padu by například přepínal mezi různou telemetrií na obrazovce, zatímco analogový joystick by ovládal samotné letadlo.

\chapter{Budoucnost projektu}

Bohužel vývoj práce byl překvapivě komplikovaný a řada původní zamýšlených vlastností nebyla implementována.

Výrazně by měla být přepracována stránka vykreslování na obrazovku -- grafický výstup je nyní relativně nevzhledný.
Grafické prostředí by také mělo mít zakomponované další indikátory, jako je směrový gyroskop či ukazatel rychlosti.

\section{Další možné vlastnosti}

Následující sekce uvádí další vlastnosti, které dron může implementovat a v budoucnu pravděpodobně bude.

\subsection{Upozornění na letovou zónu}
Dle zákona o civilním letectvý by klient také měl upozornit pilota na aktuální leteckou zónu.
Bohužel oficiální stránka řízení letového provozu nemá veřejné API, existují však služby jako \url{airmap.com}, které poskytují potřebné informace.
Přidání tohoto upozornění není příliš složité, jelikož z Raspberry Pi získáváme data o poloze.

\subsection{Spojení s Assault Tactical Android Kit}

Více zajímavější by byla integrace na ATAK, respektive jeho verzi pro civilní použití -- CivTAK.
Jedná se o nástroj pro koordinaci složek v terénu vyvinutý armádou Spojených států amerických.
Vzhledem k svojí povaze nabízí relativně širokou škálu možností, jak začlenit do širšího systému autonomního drona.
Existuje navíc open source software FreeTAKServer, který poskytuje REST API na použití těchto funkcí.
I přes poměrně dobrou dokumentaci je celý systém velmi složitý a propracované propojení by bylo velmi časově náročné.

\subsection{Autopilot}

V aktuální verzi implementuje projekt jednoduchého autopilota, který je schopen držet letový kurz.
Neudržuje však aktuální nadmořskou výšku a kurz může být libovolně posunut ve směru lineárně závislém s aktuálním směrem.
Letadlo se tak postupem času výrazně odchýlí od svého původního směru.

Již v jádru práce bylo navrhnuto řešení pro tento problém.
Teoreticky by toto řešení mohlo být rozšířeno v plnohodnotného autopilota, který by byl schopen vždy dorazit na danou pozici.
S autonomním letem souvislý i možnost letu na vzdálenost větší, než co umožní komunikace.
Dron by tak měl mít možnost ukládat video, či pořizovat snímky.

\subsection{Stabilnější forma přenosu dat}

V aktuální verzi se Raspberry Pi chová jako Wi-Fi Access Point.
Dosah systému je sice dostačující -- Raspberry má 5Dbi všesměrovou anténu přijímač 25Dbi Yagi anténu, ale slabý signál na delších vzdálenostech představuje problém.
Situace by se dala teoreticky dala řešit posilovačem, který by posunou sílu signálu z řádu miliwattů na watty.

Bylo by také vhodné vyvinout anténu, která dokáže letadlo sledovat.
Systém by mohl být založený na mikročipu, jako je ESP32.
Ten by byl zinicializován se svojí polohou a orientací.
Relativně jednoduše by pak šla dopočítat poloha, kterou má anténa zaujmout v závislosti na datech z letadla.

\chapter*{}
\pagenumbering{roman}
\setcounter{page}{5} % text bude pokračovat v číslování římském, kde přestal na začátku souboru
\include{zaver}

\include{literatura}

\listoffigures
\openright
\end{document}

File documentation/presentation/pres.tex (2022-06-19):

\documentclass[aspectratio=43]{beamer}
\usetheme{Berlin}

\usepackage[czech]{babel}
\usecolortheme{dolphin}
\usepackage{graphicx}
\usepackage{dirtree}
\usepackage{listings}
\usepackage[T1]{fontenc}
\usepackage{lmodern}
\usepackage[utf8]{inputenc}
\usepackage{caption}
\usepackage{bbding}
\usepackage{xurl}
\usepackage{scrextend}
\usepackage{minted}
\usepackage{appendixnumberbeamer}

\captionsetup{labelformat=empty}

\beamertemplatenavigationsymbolsempty
\defbeamertemplate*{title page}{customized}[1][]
{
	\usebeamerfont{title}\inserttitle\par
	\usebeamerfont{subtitle}\usebeamercolor[fg]{subtitle}\insertsubtitle\par
	\bigskip
	\usebeamerfont{author}\insertauthor\par
	\usebeamerfont{institute}\insertinstitute\par
	\usebeamerfont{date}\insertdate\par
	\usebeamercolor[fg]{titlegraphic}\inserttitlegraphic
}

\hypersetup{unicode}
\hypersetup{breaklinks=true}

\title{Bezpilotní letadlo}
\subtitle{Dron postavený na platformě Raspberry Pi}
\author{Havránek Kryštof 4.E}
\date{Březnen 2022}
\institute{Gymnázium, Praha 6, Arabská 14}
\setbeamertemplate{sidebar right}{}
\setbeamertemplate{footline}{%
\hfill\textbf{Stránka \insertframenumber{}. z \inserttotalframenumber} \hspace{0.01cm} \vspace{0.1cm}}
\setbeamerfont{footnote}{size=\tiny}

\begin{document}

\begin{frame}[plain]
	\maketitle
\end{frame}

\clearpage
\setcounter{framenumber}{0}

\begin{frame}[fragile]
	\frametitle{Úvod}
	\section{Úvod}

	\begin{itemize}
		\item Bezpilotní letadlo a jeho dobrovolný systém -- dálkové řízené, přenos videa a telemetrie
		\item Řízení přes Xbox ovladač
		\item Proč jsem si téma vybral?
		\item Kód dostupný na GitHubu pod licencí MIT (včetně knihoven)
		\item Linux + Raspbian, port ovládacího softwaru je možný
	\end{itemize}
\end{frame}

\begin{frame}[fragile]
	\frametitle{Protokol}
	\begin{itemize}
		\item Komunikace prostřednictvím protokolu postaveném na rodině TCP
		\item Video předáváno přes UDP (gstreamer)
		\item Protokol navržený pro potřeby práce -- tři základní funkce -- telemetrie, ovládání a nastavení
		\item Předávání struktur
		\item Raspberry Pi -- server, Pilot -- klient
		\item Podpora více ovládacích stanic
	\end{itemize}
\end{frame}

\begin{frame}[fragile]
	\frametitle{Design letadla}
	\section{Design letadla}
	\begin{itemize}
		\item Založeno na kostře Mini Talon od společnosti X-UAV
			\begin{itemize}
				\item Rozpětí křídel: 130cm
				\item Délka: 85cm
				\item Vzletová váha: 1.5 kg
			\end{itemize}
		\item Délka letu nad 1 hodinu
		\item Jádro -- Raspberry Pi Zero 2
		\item Doprovázen řadou periférií
	\end{itemize}
\end{frame}

\begin{frame}[fragile]
	\frametitle{Design letadla}
	\begin{figure}[h]
		\centering
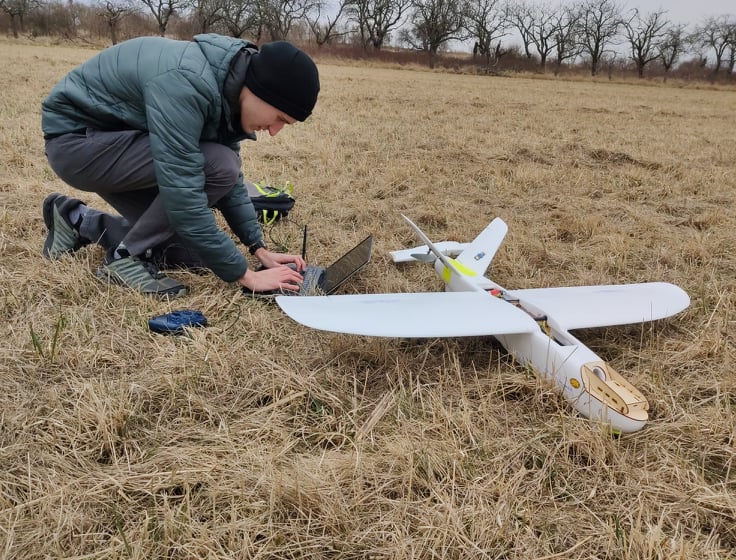
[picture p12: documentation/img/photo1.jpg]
		
	\end{figure}
\end{frame}

\begin{frame}[fragile]
	\frametitle{Design letadla}
	\begin{figure}[h]
		\centering
		
	\end{figure}
\end{frame}

\begin{frame}[fragile]
	\frametitle{Periférie}
	\begin{itemize}
		\item Wit-Motion WT901B
			\begin{itemize}
				\item Devíti osý polohový senzor
				\item Údaje o orientaci v prostoru, teplotě, zrychlení
				\item Slouží k fungování autopilota
			\end{itemize}
		\item INA226
			\begin{itemize}
				\item Voltmetr/ampérmetr
				\item Měří odběr celého letadla a napětí na baterii
			\end{itemize}
	\end{itemize}
\end{frame}

\begin{frame}[fragile]
	\frametitle{Periférie}
	\begin{itemize}
		\item ublox NEO 7M
			\begin{itemize}
				\item GPS modul
				\item Údaje o poloze a nadmořské výšce
			\end{itemize}
		\item PCA9865
			\begin{itemize}
				\item Modul na ovládání servo motorů
				\item Připojen na ESC (Beatles 40A) -- ovládá rychlost hlavního motoru
			\end{itemize}
	\end{itemize}
\end{frame}

\begin{frame}[fragile]
	\frametitle{Zapojení}
	\begin{figure}[h]
		\centering
		
	\end{figure}
\end{frame}

\begin{frame}[fragile]
	\frametitle{Zapojení}
	\begin{figure}[h]
		\centering
		
	\end{figure}
\end{frame}

\begin{frame}[fragile]
	\frametitle{Program letadla}
	\begin{itemize}
		\item Se senzory se komunikuje prostřednictvím knihoven
			\begin{itemize}
				\item 3 forknuté a přepsané knihovny
				\item V programu se přistupuje přes singletony
			\end{itemize}
		\item Stream z kamery je aktuálně spuštěn programem v podprocesu
		\item Za standardního provozu se letadlo řídí pokyny pilota
		\item Čekání na zprávu $\Rightarrow$ vyhodnocení $\Rightarrow$ thread pool zpracuje
		\item Letadlo je schopno držet svojí letovou hladinu -- dva PID kontroléry
	\end{itemize}
\end{frame}

\begin{frame}[fragile]
	\frametitle{Ovládací software}
	\section{Ovládací software}
	\begin{itemize}
		\item Vyvíjen pro operační systém Linux
		\item Postavený na grafickém toolkitu Gtk3
		\item Zpracování dat z ovladače, zobrazení videa a telemetrie
		\item Ovladač
			\begin{itemize}
				\item Použit návrhový vzor observeru -- interface s ovladačem generuje události
				\item Nemusí tak existovat centrální organizační bod
				\item Odeslání příkazů letadlu, ovládání uživatelského prostředí
			\end{itemize}
	\end{itemize}
\end{frame}

\begin{frame}[fragile]
	\frametitle{Ovládací software}
	\begin{figure}[h]
		\centering
		
	\end{figure}
\end{frame}

\begin{frame}[fragile]
	\frametitle{Závěr}
	\section{Závěr}
	\begin{itemize}
		\item Cíl práce byl splněn
		\item Práce však nebyla realizována v původně zamýšleném rozsahu
		\item Řada problémů, kritický nedostatek znalostí
	\end{itemize}
\end{frame}

\begin{frame}[fragile]
	\frametitle{Budoucnost Projektu}
	\begin{itemize}
		\item Upozornění na letovou zónu
		\item Spojení s ATAK
		\item Autopilot
		\item Přechod od Wi-Fi, rezervní spojení?
		\item Doprovodný hardware -- tracking anténa, katapult
	\end{itemize}
\end{frame}

\appendix
\begin{frame}[plain]
	\centering
	\Huge Dotazy?
\end{frame}

\end{document}

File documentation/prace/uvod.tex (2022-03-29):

\chapter*{Úvod}
\addcontentsline{toc}{chapter}{Úvod}

Cílem práce bylo sestavit bezpilotní letadlo a napsat doprovodný software -- a to jak pro samotný dron, tak počítač, který letadlo ovládá.
Uživatel sytému by měl mít možnost sledovat video stream z letadla a letadlo dálkově ovládat.
Programová část kódu by měla být psána v souladu s klasickými návrhovými vzory a umožňovat jednoduchou implementaci dalších funkcí.

Dron je postavený okolo malého počítače Raspberry Pi Zero 2, ke kterému jsou připojeny ostatní periférie přes sériovou a I2C linku.
Komunikace mezi dronem a pilotem probíhá přes TCP protokol.
Raspberry Pi tak funguje jako Access Point.
Konfigurační soubory pro nastavení Access Pointu jsou přiložené u kódu.

Celý kód práce je dostupný na Github pod licencí MIT -- \url{https://github.com/havrak/UAV-project}.
V rámci práce na projektu byly napsány tři doprovodné knihovny -- \url{https://github.com/havrak/Raspberry-JY901-Serial-I2C}, \url{https://github.com/havrak/raspberry-pi-ina226} a \url{https://github.com/havrak/PCA9685-rpi}.
Všechny jsou volně dostupné k použití také pod licencí MIT.

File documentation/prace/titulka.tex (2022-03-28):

%%% Titulní strana práce

\pagestyle{empty}
\hypersetup{pageanchor=false}

\begin{center}

{\LARGE\bfseries\NazevSkoly}

\vspace{-18mm}
\vfill

{\LARGE\NazevOboru}

\vfill

\centerline{\mbox{\def\svgwidth{\columnwidth}\scalebox{0.25}{\input{../img/logo.pdf_tex}}}}

\vspace{-8mm}
\vfill

{\bf\Large MATURITNÍ PRÁCE}

\vfill

\vspace{15mm}

{\LARGE\bfseries\NazevPrace}

\vfill

Vypracoval: \hfill \AutorPrace

Vedoucí práce: \hfill \Vedouci

\vspace{15mm}
\MesicOdevzdani \ \RokOdevzdani

\end{center}

\newpage
\hypersetup{pageanchor=true}
\pagestyle{plain}
\pagenumbering{roman}

\openright

\vspace*{\fill}

\noindent
Prohlašuji, že jsem jediným autorem této práce, všechny citace jsou
řádně označené a všechna použitá literatura a další zdroje jsou v práci uvedené.
Tímto dle zákona 121/2000 Sb. (tzv. Autorský zákon) ve znění pozdějších předpisů uděluji
bezúplatně škole Gymnázium, Praha 6, Arabská 14 oprávnění k výkonu práva na rozmnožování díla
(§ 13) a práva na sdělování díla veřejnosti (§ 18) na dobu časově neomezenou a bez omezení
územního rozsahu.

\vspace{1cm}

\noindent
V ........ dne ............
\hspace{4cm}
Podpis autora

\newpage

\openright

\vbox to 0.20\vsize{
\setlength\parindent{0mm}
\setlength\parskip{5mm}

Název práce:
\NazevPrace

Autor:
\AutorPrace

% Vedoucí práce:
% \Vedouci, \KatedraVedouciho

Abstrakt:
\Abstrakt

Klíčová slova:
\KlicovaSlova

% Opakování v angličtině.
\noindent\rule{7cm}{0.4pt}

Title:
\NazevPraceEN

Author:
\AutorPrace

Abstract:
\AbstraktEN

Key words:
\KlicovaSlovaEN

% Opakování v němčině.
\noindent\rule{7cm}{0.4pt}

Titlel:
\NazevPraceDE

Autor:
\AutorPrace

Abstrakt:
\AbstraktDE

Schlüsselwörter:
\KlicovaSlovaDE

\vss}

\newpage

\openright

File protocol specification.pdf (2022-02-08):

UAV Project – Protocol specification

# Protocol specification

- protocol desing

– 1st byte – type of message

– 2nd byte – priority of message (for now for messages with higher priority than 0 new thread will be created)

– 3rd and 4th byte – gives information about size of message – 3rd is 8 higher bytes, 4th is lower 8 bytes

– 5 – value to be added to check sum – first 5 bytes need to be divisible by 7

– ... – message

– each message is terminated with following sequence – 0x00, 0x00, 0xFF, 0xFF, 0xFF

- ranges

– 0x00 – 0x20 – settings management

– 0x21 – 0x40 – control

– 0x41 – 0xFF – telemetry

- * symbol means code is only used as get request/confirmation
- structures used are specified in <protocol_spec.h>

Settings

0x01 | PI+CL | ping – empty message send by both sides
0x02 | CL | restart of system
0x03 | CL | shutdown
0x04 | CL | disconnect client
0x08 | CL | camera settings

Control

- these messages are only send by the client to raspberry pi
- standart control message will be send continuously – every few milliseconds (client will have counter to prevent overloading of the server)
- we are fine with few of these messages getting lost, as even minor movements will probably result in new message getting send
- special message will send confirmation to the client

– client will add these messages to queue, which will be scanned from time to time

– if response from server wasn’t received in some time client will resend the message

Havránek Kryštof <krystof@havrak.xyz> | 1

UAV Project – Protocol specification

0x21 | CL+PI* | standart control message – status of analog joystick and shoulder buttons
0x22 | CL+PI* | special control event – generated by pressing buttons that don’t directly control control surfaces, but are free for further additions

Telemetry

- all telemetry, except pwm settings, is send in intervals
- if client want new data immediately it can send message with same header
- in such case using priority option is advisable
- range above 0x80 is used for errors
0x41 | PI*+CL | status of all i/o
0x42 | PI*+CL | general packet including all information
0x43 | PI*+CL | attitude sensor and GPS
0x44 | PI*+CL | battery status (reading from ina226)
0x45 | PI*+CL | pwm setting on servo driver
0x81 | PI | general error message
Havránek Kryštof <krystof@havrak.xyz> | 2

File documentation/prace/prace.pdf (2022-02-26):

# Gymnázium, Praha 6, Arabská 14

# Programování

## ROČNÍKOVÝ PROJEKT

# Bezpilotní letadlo

Vypracovali: | Havránek Kryštof
Vedoucí práce: | ing. Daniel Kahoun

Únor 2022

Ročníková práce – Gymnázium, Praha 6, Arabská 14 | Bezpilotní letadlo

Prohlašujeme, že jsem jediným autorem tohoto projektu, všechny citace jsou řádně

označené a všechna použitá literatura a další zdroje jsou v práci uvedené. Tímto dle

zákona 121/2000 Sb. (tzv. Autorský zákon) ve znění pozdějších předpisů uděluji bez-

úplatně škole Gymnázium, Praha 6, Arabská 14 oprávnění k výkonu práva na rozmno-

žování díla (§ 13) a práva na sdělování díla veřejnosti (§ 18) na dobu časově neomezenou

a bez omezení územního rozsahu.

V ........ dne | | Podpis autora
Vypracoval: Havránek Kryštof(Programování) | i

Název práce: Bezpilotní letadlo

Autor: Havránek Kryštof

Abstrakt:

Klíčová slova: (UAV), (Gtk), (C++), (Raspberry zero 2)

Title: Drone

Author: Havránek Kryštof

Abstract:

Key words: (UAV), (Gtk), (C++), (Raspberry zero 2)

Titlel: Drohne

Autor: Havránek Kryštof

Abstrakt:

Schlüsselwörter: (UAV), (Gtk), (C++), (Raspberry zero 2)

Vypracoval: Havránek Kryštof(Programování) | ii

# Obsah

Úvod | iv
1 Rozložení práce | 1
2 Hardware a Raspberry Pi | 2
3 Client na ovládání | 3
Závěr | vi
Seznam použité literatury | vii
Seznam obrázků | viii
Vypracoval: Havránek Kryštof(Programování) | iii

# Úvod

Vypracoval: Havránek Kryštof(Programování) | iv

# 1. Rozložení práce

Práci lze rozdělit na dva základní komponenty. První část software běží na počítači

přes který se bezpilotní letadlo ovládá, druhá na samotném dronu. Obě části jsou psané

v jazyce C++.

Software pro počítač používá grafickou knihovnu Gtk3 a byl vyvíjen primárně na

operačním systém Linux. Gtk3 je multiplatformní toolkit, port na další operační sys-

témy je tak možný a kód je psán stylem, aby umožnil další verze.

Jádro samotného dronu představuje malý počítač Raspberry Pi Zero 2. Vyšší výkon

verze Zero verze 2 není nutný pro fungování, práce tak defacto může fungovat na

libovolném Raspberry Pi.

Obě části mezi sebou komunikují prostřednictvím protitoku založené na TCP ro-

dině. Přenos videa je zprostředkovávám pomocí UDP.

## 1.1 Komunikační protokol

Vypracoval: Havránek Kryštof(Programování) | 1

# 2. Hardware a Raspberry Pi

Vypracoval: Havránek Kryštof(Programování) | 2

# 3. Client na ovládání

Vypracoval: Havránek Kryštof(Programování) | 3

# Závěr

Vypracoval: Havránek Kryštof(Programování) | vi

# Seznam použité literatury

Vypracoval: Havránek Kryštof(Programování) | vii

# Seznam obrázků

Vypracoval: Havránek Kryštof(Programování) | viii

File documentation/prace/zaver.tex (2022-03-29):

\chapter*{Závěr}
\addcontentsline{toc}{chapter}{Závěr}

Cíl práce specifikovaný v zadání byl splněn.
Letadlo je schopné letu a uživatel má k dispozici stream z kamery na dronu.

Práci však komplikovala řada problémů a to jak s hardwarem, tak se softwarem.
Před začátkem jsem měl jen velmi povrchní zkušenosti s jazykem C++ a žádné s jak Gtk3, tak vývojem pro Raspberry Pi.
Práce tak nemohla být realizována tak, jak byla původně zamýšlena.

Tomu napovídá i dlouhý list s budoucností projektu.
Ačkoliv tomu samotné řádky kódu nemusí napovídat, práce mi dala celou řadu nových znalostí.
I proto plánuji dále na projektu pokračovat ve svém volém čase.
Rád bych systém dostal do stavu, kdy se jedná o plnohodnotnou realizaci bezpilotního systému.

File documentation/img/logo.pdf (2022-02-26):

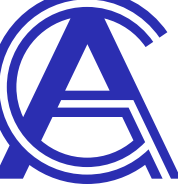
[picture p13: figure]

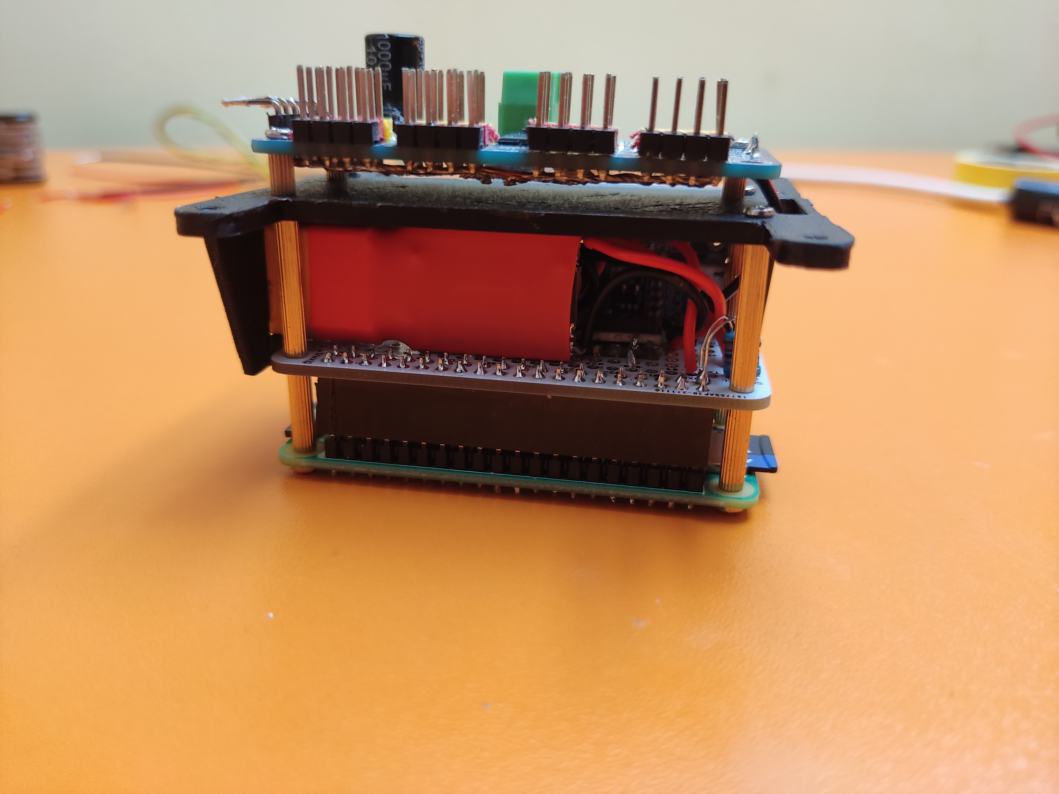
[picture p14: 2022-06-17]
photos/detail_2.jpg

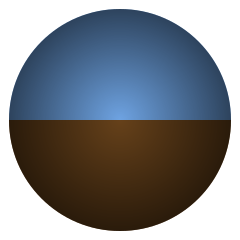
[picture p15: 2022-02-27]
desktop client/images/ai_back.png

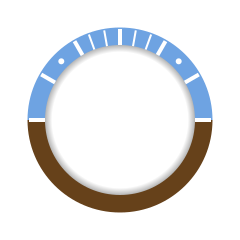
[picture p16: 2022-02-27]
desktop client/images/ai_ring.png

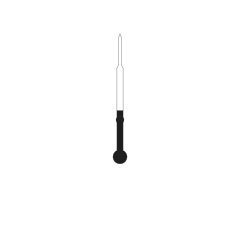
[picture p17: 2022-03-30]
desktop client/images/asi_hand.png

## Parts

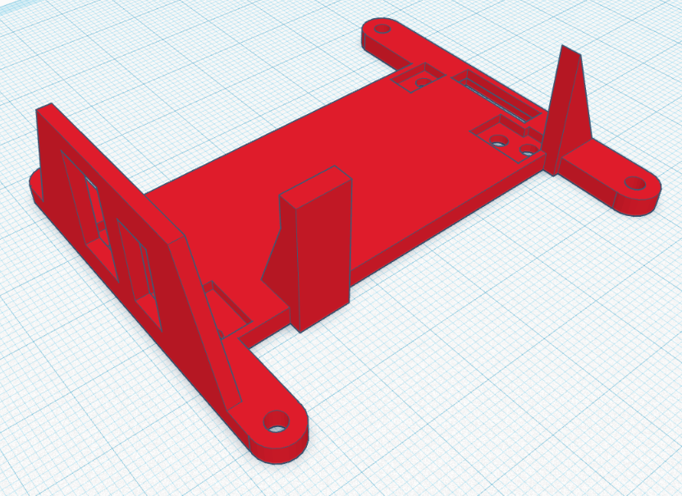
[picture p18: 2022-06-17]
stl files/Copy of Plane components mount.png

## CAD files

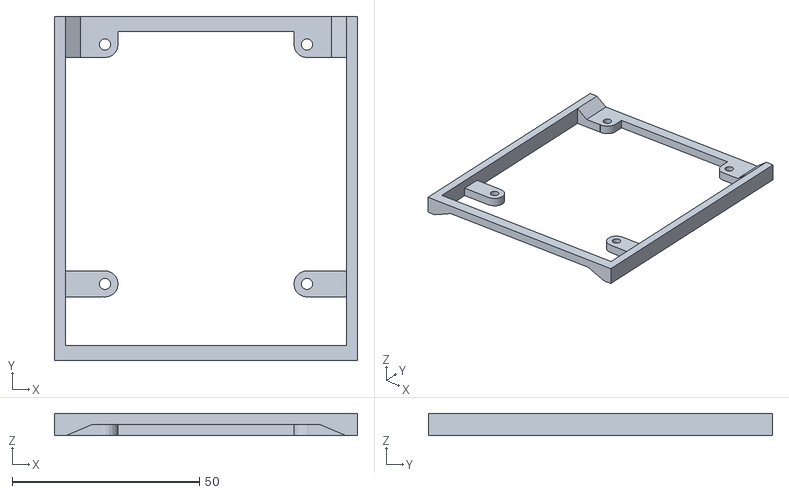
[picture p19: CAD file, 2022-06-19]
stl files/insert into plane fuselage.stl
81.0 x 92.0 x 6.00

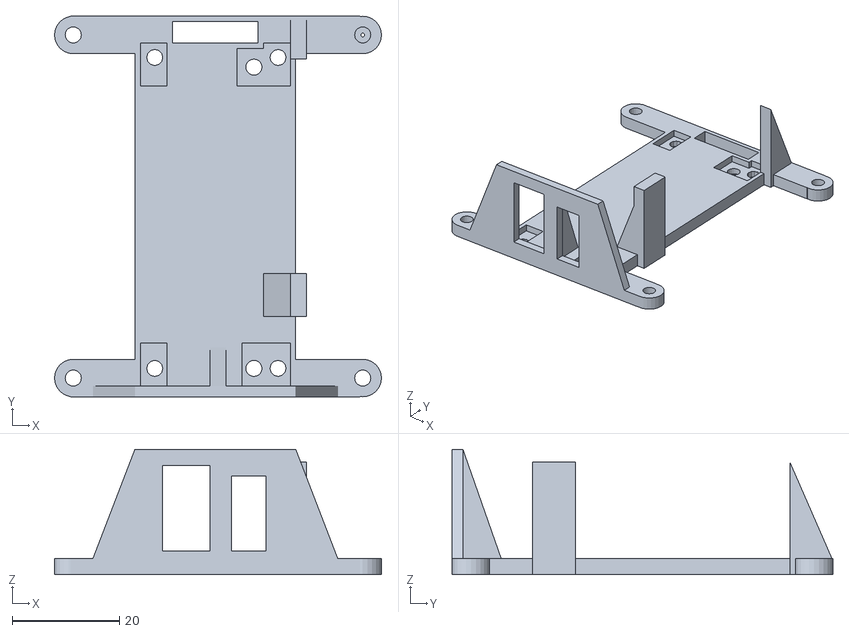
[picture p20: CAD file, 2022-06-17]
stl files/Copy of Plane components mount.stl
61.0 x 71.0 x 23.4

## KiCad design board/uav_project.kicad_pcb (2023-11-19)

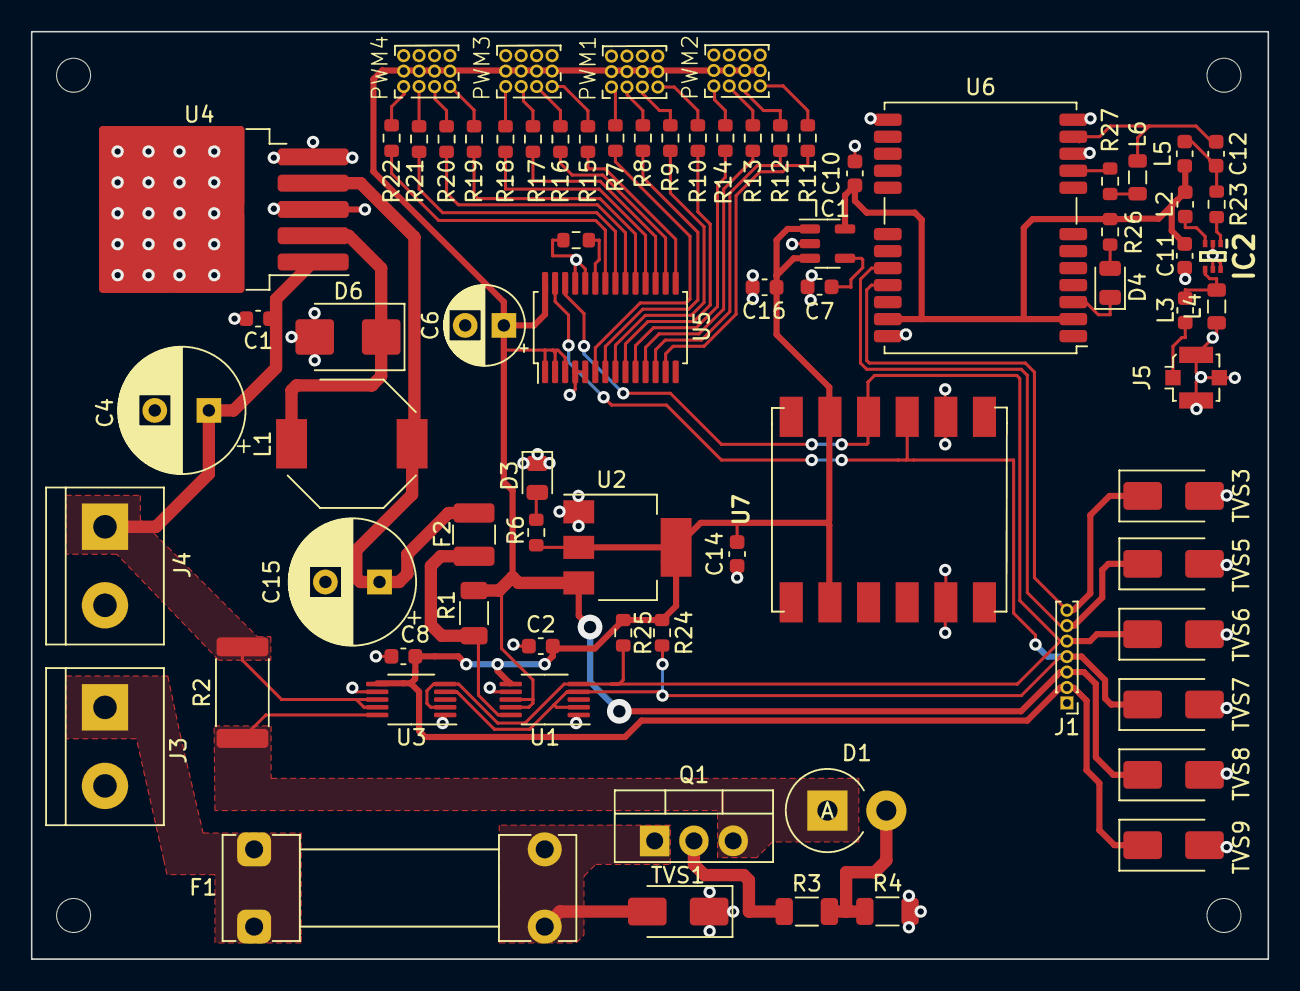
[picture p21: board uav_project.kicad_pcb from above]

Board: 2 copper layers, 80.0 x 60.0 mm, 80 parts (0 on the bottom side), 61 nets.

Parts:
C1, C2, C7, C8, C11, C14: 100n; C_0603_1608Metric
C4, C15: 100u; CP_Radial_D8.0mm_P3.50mm
C6: 33u; CP_Radial_D5.0mm_P2.50mm
C10, C16: 1p; C_0603_1608Metric
C12: 100p; C_0603_1608Metric
D1: 1N53xxB; D_DO-201_P3.81mm_Vertical_AnodeUp
D3, D4: LED; LED_0805_2012Metric
D6: SS210; D_SMB
F1: Fuse; Fuseholder_Clip-5x20mm_Littelfuse_111_Lateral_P18.80x5.00mm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
F2: Polyfuse; Fuse_1210_3225Metric
H1, H2, H3, H4: MountingHole; MountingHole_2.2mm_M2
IC1: RT9193-33GB; SOT-23-5
IC2: NJG1130KA1-TE1; SOTFL50P160X60-6N
J1: Conn_01x07; PinHeader_1x07_P1.00mm_Vertical
J3: Bat IN Terminal; TerminalBlock_bornier-2_P5.08mm
J4: Bat OUT Terminal; TerminalBlock_bornier-2_P5.08mm
J5: Conn_Coaxial; U.FL_Molex_MCRF_73412-0110_Vertical
L1: 47u; L_Bourns-SRU8043
L2, L3: 8.7n; L_0603_1608Metric
L4, L6: 18n; L_0805_2012Metric
L5: 47n; L_0603_1608Metric
PWM1, PWM2, PWM3, PWM4: conn_03x04_Pin; PinHeader_3x04
Q1: PMOS; TO-220-3_Vertical
R1: 20m; R_1206_3216Metric
R2: 20m; R_2512_6332Metric
R3: 100; R_1206_3216Metric
R4: 10k; R_1206_3216Metric
R5: 10k; R_0603_1608Metric
R6, R26: 470; R_0603_1608Metric
R7, R8, R9, R10, R11, R12, R13, R14, R15, R16, R17, R18, R19, R20, R21, R22: 220; R_0603_1608Metric
R23, R27: 10; R_0603_1608Metric
R24, R25: 4.7k; R_0603_1608Metric
TVS1, TVS3, TVS5, TVS6, TVS7, TVS8, TVS9: SMAJ30CA; D_SMA
U1, U3: INA226; VSSOP-10_3x3mm_P0.5mm
U2: AMS1117-3.3; SOT-223-3_TabPin2
U4: LM2596S-5; TO-263-5_TabPin3
U5: PCA9685PW; TSSOP-28_4.4x9.7mm_P0.65mm
U6: NEO-M7N; ublox_NEO
U7: WT901B

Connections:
+3V3: C2.1, C8.1, C14.1, C16.2, IC1.1 (VIN), IC1.3 (EN), J1.2, R6.1, R24.1, R25.1, TVS9.1 (A1), U1.6 (VS), U2.2 (VO), U3.6 (VS), U7.2 (VCC)
+5V: C6.1, J1.3, PWM1.2, PWM1.5, PWM1.8, PWM1.11, PWM2.2, PWM2.5, PWM2.8, PWM2.11, PWM3.2, PWM3.5, PWM3.8, PWM3.11, PWM4.2, PWM4.5, PWM4.8, PWM4.11, R1.2, TVS8.1 (A1), U1.8 (Vbus), U1.9 (Vin-), U2.3 (VI), U5.1 (A0), U5.2 (A1), U5.3 (A2), U5.28 (VDD)
/GPS module/+3V3 LN: C10.2, C11.1, IC1.5 (VOUT), L2.1, L5.1, R26.2, U6.2 (D_SEL), U6.23 (VCC)
/GPS module/RF_IN: C12.1, L6.2, U6.11 (RF_IN)
/GPS module/VCC_RF: R27.2, U6.9 (VCC_RF)
/Power managment/5V SENSE IN: F2.2, R1.1, U1.10 (Vin+)
/Power managment/BAT SENSE IN: D1.1 (K), Q1.3 (S), R2.1, U3.10 (Vin+)
/Power managment/BAT SENSE OUT: C1.1, C4.1, J4.1, R2.2, U3.8 (Vbus), U3.9 (Vin-), U4.1 (VIN)
/Power managment/BAT UNSAFE: F1.1, F1.2, J3.1, Q1.1 (D), TVS1.2 (A2)
/Servo driver/PWM0: R7.2, U5.6 (LED0)
/Servo driver/PWM1: R8.2, U5.7 (LED1)
/Servo driver/PWM2: R9.2, U5.8 (LED2)
/Servo driver/PWM3: R10.2, U5.9 (LED3)
/Servo driver/PWM4: R14.2, U5.10 (LED4)
/Servo driver/PWM5: R13.2, U5.11 (LED5)
/Servo driver/PWM6: R12.2, U5.12 (LED6)
/Servo driver/PWM7: R11.2, U5.13 (LED7)
/Servo driver/PWM8: R15.2, U5.15 (LED8)
/Servo driver/PWM9: R16.2, U5.16 (LED9)
/Servo driver/PWM10: R17.2, U5.17 (LED10)
/Servo driver/PWM11: R18.2, U5.18 (LED11)
/Servo driver/PWM12: R19.2, U5.19 (LED12)
/Servo driver/PWM13: R20.2, U5.20 (LED13)
/Servo driver/PWM14: R21.2, U5.21 (LED14)
/Servo driver/PWM15: R22.2, U5.22 (LED15)
GND: C1.2, C2.2, C4.2, C6.2, C7.1, C8.2, C10.1, C11.2, C14.2, C15.2, C16.1, D3.1 (K), D6.2 (A), IC1.2 (GND), IC2.2 (GND_1), IC2.5 (GND_2), IC2.6 (GND_3), J1.1, J3.2, J4.2, J5.2 (Ext), L4.1, PWM1.3, PWM1.6, PWM1.9, PWM1.12, PWM2.3, PWM2.6, PWM2.9, PWM2.12, PWM3.3, PWM3.6, PWM3.9, PWM3.12, PWM4.3, PWM4.6, PWM4.9, PWM4.12, R4.2, R5.1, TVS1.1 (A1), TVS3.2 (A2), TVS5.2 (A2), TVS6.2 (A2), TVS7.2 (A2), TVS8.2 (A2), TVS9.2 (A2), U1.1 (A1), U1.7 (GND), U2.1 (GND), U3.1 (A1), U3.7 (GND), U4.3 (GND), U4.5 (~ON/OFF), U5.4 (A3), U5.5 (A4), U5.24 (A5), U5.25 (EXTCLK), U6.10 (GND), U6.12 (GND), U6.13 (GND), U6.24 (GND), U7.5 (GND)
unnamed: C12.2, L5.2, R23.1
unnamed: D1.2 (A), R3.2, R4.1
unnamed: D3.2 (A), R6.2
unnamed: D4.2 (A), R26.1
unnamed: D4.1 (K), U6.3 (TIMEPULSE)
unnamed: D6.1 (K), L1.1, U4.2 (OUT)
unnamed: C7.2, IC1.4 (BP)
unnamed: IC2.4 (RF_IN), L3.1, L4.2
unnamed: IC2.1 (RF_OUT), R23.2
unnamed: IC2.3 (VDD), L2.2
unnamed: J5.1 (In), L3.2
unnamed: L6.1, R27.1
unnamed: PWM1.1, R7.1
unnamed: PWM1.4, R8.1
unnamed: PWM1.7, R9.1
unnamed: PWM1.10, R10.1
unnamed: PWM2.1, R14.1
unnamed: PWM2.4, R13.1
unnamed: PWM2.7, R12.1
unnamed: PWM2.10, R11.1
unnamed: PWM3.1, R18.1
unnamed: PWM3.4, R17.1
unnamed: PWM3.7, R16.1
unnamed: PWM3.10, R15.1
unnamed: PWM4.1, R22.1
unnamed: PWM4.4, R21.1
unnamed: PWM4.7, R20.1
unnamed: PWM4.10, R19.1
unnamed: Q1.2 (G), R3.1
unnamed: C15.1, F2.1, L1.2, U4.4 (FB)
unnamed: R5.2, U5.23 (~OE)
RX: J1.7, TVS3.1 (A1), U6.21 (RXD/SPI_MOSI)
SDA: J1.4, R24.2, TVS7.1 (A1), U1.2 (A0), U1.4 (SDA), U3.4 (SDA), U5.27 (SDA), U7.9 (SDA)
SLC: J1.5, R25.2, TVS6.1 (A1), U1.5 (SCL), U3.2 (A0), U3.5 (SCL), U5.26 (SCL), U7.8 (SLC)
TX: J1.6, TVS5.1 (A1), U6.20 (TXD/SPI_MISO)

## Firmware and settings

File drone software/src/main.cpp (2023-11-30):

/*
 * main.cpp
 * Copyright (C) 2021 Havránek Kryštof <krystof@havrak.xyz>
 *
 * Distributed under terms of the MIT license.
 */

#include <wiringPi.h>

#include "communication_interface.h"
#include "config.h"
#include "peripherials_manager.h"
#include <cstring>
#include <iostream>
#include <csignal>

using namespace std;

void signalHandler( int sigNum){
	cout << "MAIN | signalHandler | caught signal slowing down\n";
	CommunicationInterface::GetInstance()->cleanUp();
	PeripherialsManager::GetInstance()->servoControllMin();
	this_thread::sleep_for(chrono::milliseconds(10));
	exit(127);
}

int main(int argc, char** argv)
{
	cout << "WARNING: This program relyes on command i2cdetect to detect the I2C bus. This command cannot be executed without sudo privileges. To run the program add i2cdetect to your /etc/sudoers file\n\n";


	signal(SIGKILL, signalHandler);
	signal(SIGPIPE, SIG_IGN);
	Config config;
	config.loadConfiguration();

	cout << "MAIN | main | initializing peripherials" << endl;

	// TODO: peripherals should be created here and added to the peripherials manager
	PeripherialsManager::GetInstance()->initializePeripherials(config.getINABatAddress(), config.getINA5VAddress(), config.getPCA9865Address(), config.getIMUAddress());

	// NOTE: this is not the right place to setup INA226
	PeripherialsManager::GetInstance()->setupINA(config.getINABatShunt(), config.getINA5VShunt());

	cout << "MAIN | main | initializing servo" << endl;
	bool suppressArming = false; // don't want to wait 8 second for servos to arm
	if (argc > 1){
		if(strcmp(argv[1], "-r") == 0){
			cout << "MAIN | main | calirating ESC" << endl;
			PeripherialsManager::GetInstance()->servoControllCalibrate();
			return 1;
		}
		if(strcmp(argv[1], "-a") == 0)
				suppressArming = true;
	}

	if(!suppressArming) PeripherialsManager::GetInstance()->servoControllArm();

	cout << "MAIN | main | starting communication interface" << endl;
	CommunicationInterface::GetInstance()->setupSocket(config.getMyIP(), config.getServerPort());

	CommunicationInterface::GetInstance()->checkForNewDataThread.join();
	return 1;
}

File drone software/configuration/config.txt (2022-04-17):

# For more options and information see
# http://rpf.io/configtxt
# Some settings may impact device functionality. See link above for details

# uncomment if you get no picture on HDMI for a default "safe" mode
G#hdmi_safe=1

# uncomment this if your display has a black border of unused pixels visible
# and your display can output without overscan
#disable_overscan=1

# uncomment the following to adjust overscan. Use positive numbers if console
# goes off screen, and negative if there is too much border
#overscan_left=16
#overscan_right=16
#overscan_top=16
#overscan_bottom=16

# uncomment to force a console size. By default it will be display's size minus
# overscan.
#framebuffer_width=1280
#framebuffer_height=720

# uncomment if hdmi display is not detected and composite is being output
#hdmi_force_hotplug=1

# uncomment to force a specific HDMI mode (this will force VGA)
#hdmi_group=1
#hdmi_mode=1

# uncomment to force a HDMI mode rather than DVI. This can make audio work in
# DMT (computer monitor) modes
#hdmi_drive=2

# uncomment to increase signal to HDMI, if you have interference, blanking, or
# no display
#config_hdmi_boost=4

# uncomment for composite PAL
#sdtv_mode=2

#uncomment to overclock the arm. 700 MHz is the default.
#arm_freq=800

# Uncomment some or all of these to enable the optional hardware interfaces
dtparam=i2c_arm=on
#dtparam=i2s=on
#dtparam=spi=on

# Uncomment this to enable infrared communication.
#dtoverlay=gpio-ir,gpio_pin=17
#dtoverlay=gpio-ir-tx,gpio_pin=18

# Additional overlays and parameters are documented /boot/overlays/README

# Enable audio (loads snd_bcm2835)
dtparam=audio=on

[pi4]
# Enable DRM VC4 V3D driver on top of the dispmanx display stack
dtoverlay=vc4-fkms-v3d
max_framebuffers=2

[all]
dtoverlay=dwc2
start_x=1
gpu_mem=128
enable_uart=1
dtparam=i2c_arm=on,i2c_arm_baudrate=200000

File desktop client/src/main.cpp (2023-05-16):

/*
 * main.cpp
 * Copyright (C) 2021 Havránek Kryštof <krystof@havrak.xyz>
 *
 * Distributed under terms of the MIT license.
 */

#include "communication_interface.h"
#include "control_interpreter.h"
#include "main_window.h"
#include "controller_interface.h"
#include "linux_controller_implementation.h"
#include "airmap_provider.h"
#include "camera.h"
#include "protocol_spec.h"
#include "config.h"
#include <csignal>
#include <gtkmm.h>
#include <iostream>
#include <stdio.h>
#include <thread>
#include <X11/Xlib.h>



using namespace std;

Glib::Dispatcher dispatcher;
mutex imageMutex;


cv::Mat frameBGR, frame, frameCorrected; // Matrix to store image from camera
cv::Size imageSize;
bool cameraInitialized = false;


MainWindow* mainWindow = nullptr;
Camera* cam = nullptr;
ControllerInterface * ci = nullptr;

void cleanup(){
	cam->closeCamera();
	ci->process= false;
	ci->terminateObservatoryAndObservers();

	CommunicationInterface::GetInstance()->cleanup();
}

void signalHandler( int sigNum){
	mainWindow->closeWindow();
	cleanup();
	exit(127);
}

int main(int argc, char** argv)
{
	signal(SIGABRT, signalHandler);
	signal(SIGKILL, signalHandler);

	XInitThreads();

	Gtk::Main app(argc, argv);
	Glib::RefPtr<Gtk::Builder> builder;
	try {
		builder = Gtk::Builder::create_from_file("main_window.glade");  // create gtk builder, load glade file
	} catch (const std::exception& p_exception) {
		cerr << p_exception.what();
	}

	builder->get_widget_derived("MainWindow", mainWindow);
	cout << "MAIN | main | GTK window created\n";

	Config config;
	config.loadConfiguration();

	CommunicationInterface::GetInstance()->setupSocket(config.getServerIP(), config.getMyIP(), config.getServerPort());
	CommunicationInterface::GetInstance()->setCameraPort(config.getCameraPort());
	cout << "MAIN | main | socket setted up \n";

	if(!config.getAirmapAPIKey().empty()){ // don't start it's internal loop to fetch data if api key was not provided
		AirmapProvider::GetInstance()->setupFetching(config.getAirmapAPIKey());
	}

	switch(config.getOperatingSystem()){
		case LINUX:
			ci = (ControllerInterface*) new LinuxControllerImplementation(config.getControllerType());
		default:
			break;
	}

	if(config.getControlEnabled())
		ci->addObserver((ControlInterpreter*) new ControllerDroneBridge);

	ci->addObserver((ControlInterpreter*) new ControllerUIBridge);

	cout << "MAIN | main | controller setted up \n";

	cam = new Camera(config.getCameraPort(), config.getMyIP());

	if (mainWindow) {

		dispatcher.connect([&]() {
			imageMutex.lock();
			mainWindow->updateImage(frame);
			imageMutex.unlock();
		});

		Gtk::Main::run(*mainWindow);

		// NOTE: cleanup after window is closed
		cleanup();
	} else {
		cerr << "MAIN | main | Failed to initialize the GUI" << endl;
	}


	return 0;
}

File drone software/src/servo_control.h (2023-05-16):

/*
 * servoControl.h
 * Copyright (C) 2021 havra <krystof@havrak.xyz>
 *
 * Distributed under terms of the MIT license.
 */

#ifndef SERVO_CONTROL_H
#define SERVO_CONTROL_H

#include "protocol_spec.h"
#define MIXING_GAIN 0.5

#define MIN_PULSE_LENGTH 200 // Minimum pulse length in µs1
#define CEN_PULSE_LENGTH 1100 // Central pulse length in µs
#define MAX_PULSE_LENGTH 2000 // Maximum pulse length in µs
#define MAX_MOTOR_PULSE_LENGTH 1400

// NOTE: current max is over 1900
#define SERVO_ACCELERATION_MULTIPLIER 5
#define LOW_CONTROLLER_AXIS_VALUE 0
#define MID_CONTROLLER_AXIS_VALUE 32767
#define MAX_CONTROLLER_AXIS_VALUE 65534
#define LEVERAGE 20;

#include "../libraries/lib-pca9685/pca9685servo.h"

#include <chrono>
#include <mutex>
#include <string>
#include <thread>

using namespace std;

/**
 * enum for configuration of plane
 */
enum WingSurfaceConfiguration{
	V_SHAPE_TAIL_WING = 1,
	STANDARD_TAIL_WING = 2,
};


/**
 * enum that list different methods joystick input can be adjusted
 */
enum ControlMethodAdjuster{
	TRIGONOMETRIC, SQUARING
};


/**
 * class handeling interfacing between
 * PCA9685 and rest of the system
 */
class ServoControl {
private:
  int fd = -1;
  const bool debug = true;
  static ServoControl *servoControl;
  static mutex mutexServoControl;
	thread pidControllerThread;
	float pitch = 0, roll = 0;

	 WingSurfaceConfiguration planeConfiguration = V_SHAPE_TAIL_WING;
	 ControlMethodAdjuster controllAdjuster = SQUARING;
	bool pca9685Up = false;
	unsigned int short mainMotorMS;

	PCA9685Servo servo = PCA9685Servo(0x40);
	int currentMotorPulse;

	struct StandardTailWingConfiguration{
		int rightFlapIndex = 1;
		int leftFlapIndex = 2;
		int rightElevatorIndex = 3;
		int leftElevatorIndex = 4;
		int rudderIndex = 5;
		unsigned int short leftFlap;
		unsigned int short rightFlap;
		unsigned int short leftElevator;
		unsigned int short rightElevator;
		unsigned int short rudder;

	};
	struct VShapeTailWingConfiguration{
		int rightFlapIndex = 4;
		int leftFlapIndex = 5;
		int rightRuddervatorIndex = 2;
		int leftRuddervatorIndex = 3;
		unsigned int short leftFlap;
		unsigned int short rightFlap;
		unsigned int short leftRuddervator;
		unsigned int short rightRuddervator;
	};

	VShapeTailWingConfiguration vTail;
	StandardTailWingConfiguration standard;

	/**
	 * adjust control of main motor new
	 * value depends on position of left
	 * and right trigger
	 *
	 * @param pConStr ps - struture from which position of triggers is extracted
	 * @return bool - true if value was set successfully
	 */
	bool adjustMainMotorSpeed(pConStr ps);

	/**
   * sets angle of given servo
	 * servos on right side are reversed, thus value of angle
	 * needs to be flipped
	 *
	 * @param int channel - on which port is servo connected
	 * @param bool right - is servo on the right side of the plane
	 * @param unsigned char angle - desired angle of servo
	 */
	void setAngleOfServo(int channel, bool right, unsigned char angle);




protected:
  ServoControl();

public:
	/**
	 * main method used to access ServoControl
	 * if instace wasn't created it will initialize
	 * ServoControl
	 */
  static ServoControl *GetInstance();

	/**
   * attaches PCA9685, runs initial configuration
	 *
	 */
	bool attachPCA9685(int address);

	/**
	 * calibrates ESC
	 * sets ms to min value and after while to max
	 * needs to be called only when using brand new ESC
	 *
	 * @return bool - true if calibration runned
	 */
  bool calibrateESC();

	/**
	 * armESC after boot, needs to be called in order to use it
	 *
	 * @return bool - true if ESC was armed
	 */
	bool armESC();

	/**
	 * slows down main motor to min speed
	 * necessary to be called before turing of the system
	 */
	void slowDownToMin();

	/**
	 * configures how controlls should be interpreted
	 *
	 * @param WingSurfaceConfiguration wsc - plane configuration
	 * @param ControlMethodAdjuster cma - method how controller input should be adjusted
	 */
	void setOperationalParameters(WingSurfaceConfiguration wsc, ControlMethodAdjuster cma);

	/**
	 * get status of PCA9685
	 *
	 * @return bool - true of PCA9685 is online
	 */
	bool getPCA9865Status();

	/**
	 * set status of PCA9685 as it is telemetry.h
	 * who checks i2c devices
	 *
	 * @param bool status - new status
	 */
	void setPCA9865Status(bool status);

	unsigned int short getMainMotorMS();

	/**
	 * returns configuration of the plane alongside angle of all control surfaces
	 *
	 * @return<int, unsigned char*> - first value corresponds to configuration second to array of angles of controll surfaces
	 */
	pair<int,unsigned char*> getControlSurfaceConfiguration();

	/**
	 * processes new control from client
	 * calls corresponding method depending
	 * on configuration of the plane
	 *
	 * @param ProcessingStructure ps - strucure with new configuration
	 * @return int - 0 if processesing went well
	 */
	bool processControl(ProcessingStructure ps);

	/**
	 * interprets controller state for V-Tail
	 *
	 * @param pConStr ps - structure with controller state
	 * @return int - 0 if processesing went well
	 */
	bool processMovementForVTail(pConStr ps);

	/**
	 * interprets controller state for standard
	 * plane configuration
	 *
	 * @param pConStr ps - structure with controller state
	 * @return int - 0 if processesing went well
	 */
	bool processMovementForStandart(pConStr  ps);
};


#endif /* !SERVOCONTROL_H */

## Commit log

2021-10-28 fucnking kill me
    [JY901.OBJ, STARTUP.OBJ, test.OBJ]
2021-10-29 small changes, nothing for drone works yet
    [JY901.OBJ, STARTUP.OBJ, test.OBJ]
2021-10-31 fixed singleton, updateLoop and CMake file
    [main.cpp]
2021-11-21 forgot to commit servoControl.h
2021-12-05 Trying to get servo to work
2022-01-14 Moved WT901 to I2C, intergrated GPS
2022-02-07 Reworkied fixing of messages via circular buffer
    [communication_interface.cpp]
2022-02-08 Added threadpool to send data
2022-02-13 Desktop client now compiles and doen't crash imediately
    [communication_interface.cpp, drone_telemetry.cpp, main.cpp]
2022-02-15 Fixed the stupid error
    [communication_interface.cpp, main.cpp]
2022-02-21 Added configuration files for rpi0
    [config.txt]
2022-02-23 Revorked error sending system
    [communication_interface.cpp, drone_telemetry.cpp, main.cpp]
2022-02-24 Fixed interaction with text buffer, rescale video
    [communication_interface.cpp, main.cpp]
2022-02-26 Started work on PID
2022-02-27 added PID controller
2022-02-28 added docs on raspberry pi side
2022-03-18 Did rewrite for camera, started implementing configuration file logic
2022-03-29 Detection of sensors now works, configurable adresses of i2c devices
2022-04-17 Found type in configuration which resulted in WT901B not working
    [config.txt]
2022-06-17 Reworked internal layout of hardware
    [Copy of Plane components mount.stl]
2022-06-19 Updated photos, eddit stl file with mount of components
    [insert into plane fuselage.stl]
2023-05-16 nuked current structure of drone side
2023-10-12 Started work on board
    [gps_module.kicad_sch, power_managment.kicad_sch, servo_driver.kicad_sch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]
2023-10-14 Hopefully finished schema for pcb
    [gps_module.kicad_sch, power_managment.kicad_sch, servo_driver.kicad_sch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]
2023-10-15 Minor changes in shchema for PCB
    [gps_module.kicad_sch, servo_driver.kicad_sch, uav_project.kicad_sch]
2023-10-15 Reverted sensor logic back from old commit
    [battery_interface.h, communication_interface.cpp, ina226_decorator.h]
2023-10-18 Updated schme to comply with electrical rules checker, prepared sensor logic for rewrite
    [gps_module.kicad_sch, power_managment.kicad_sch, servo_driver.kicad_sch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]
2023-10-22 More work in reformating drone side of codebase to be semi usable
    [gps_module.kicad_sch, power_managment.kicad_sch, servo_driver.kicad_sch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]
2023-10-24 Started work on PCB design, more work on rewritting firmware to be semi usable
    [gps_module.kicad_sch, power_managment.kicad_sch, servo_driver.kicad_sch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]
2023-10-25 More work on PCB design
    [power_managment.kicad_sch, servo_driver.kicad_sch, uav_project.kicad_pcb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]
2023-10-25 First version of PCB finished
    [gps_module.kicad_sch, power_managment.kicad_sch, servo_driver.kicad_sch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]
2023-10-27 Minor improvements to board design
    [power_managment.kicad_sch, servo_driver.kicad_sch, uav_project.kicad_pcb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]
2023-10-28 Put some more space between 16V and 5V line
    [uav_project.kicad_pcb]
2023-10-30 Cleanup on drone side, to make code more bearable and simple
    [power_managment.kicad_sch, uav_project.kicad_pcb]
2023-10-31 Minor improvement to the board
    [gps_module.kicad_sch, uav_project.kicad_pcb]
2023-11-19 Compilation on bananpi works
    [uav_project.kicad_pcb]
2023-11-19 Added BOM, changed readme
2023-11-30 Changed example of drone configuration, badly added option to set shunt value
    [power_managment.kicad_sch]
